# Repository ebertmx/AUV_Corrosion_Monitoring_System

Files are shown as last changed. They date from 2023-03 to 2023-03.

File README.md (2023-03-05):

# AUV_Corrosion_Monitoring_System
 Autonomous Corrosion Monitoring System for AUV Deployment

 See Final_Report for full project description.
 See Engineering_Analysis for engineering techniques and simulation result
 See Project_Background for intial research and motivation.

Sample Images
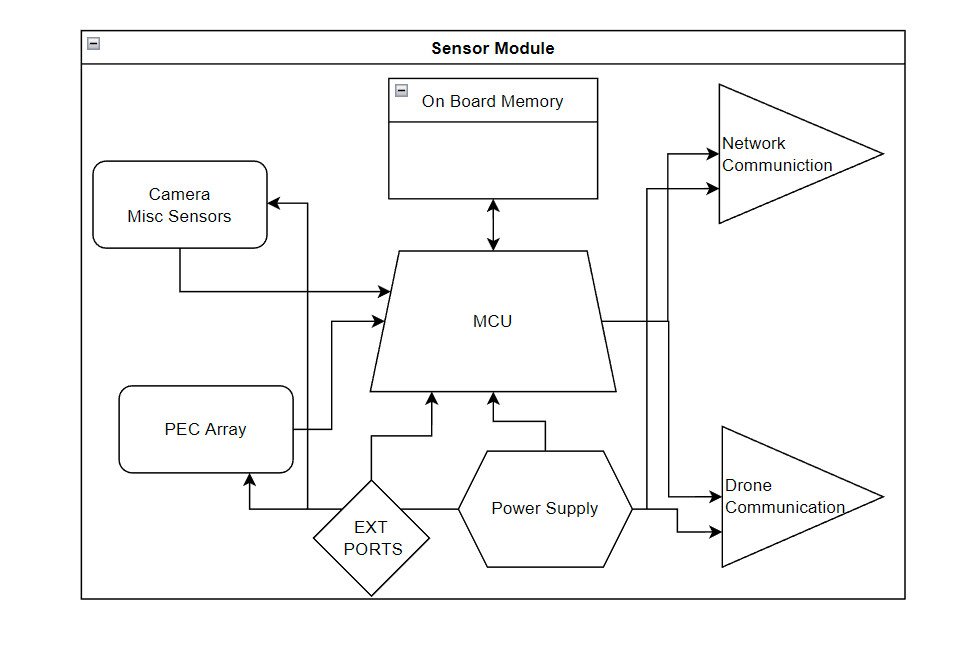
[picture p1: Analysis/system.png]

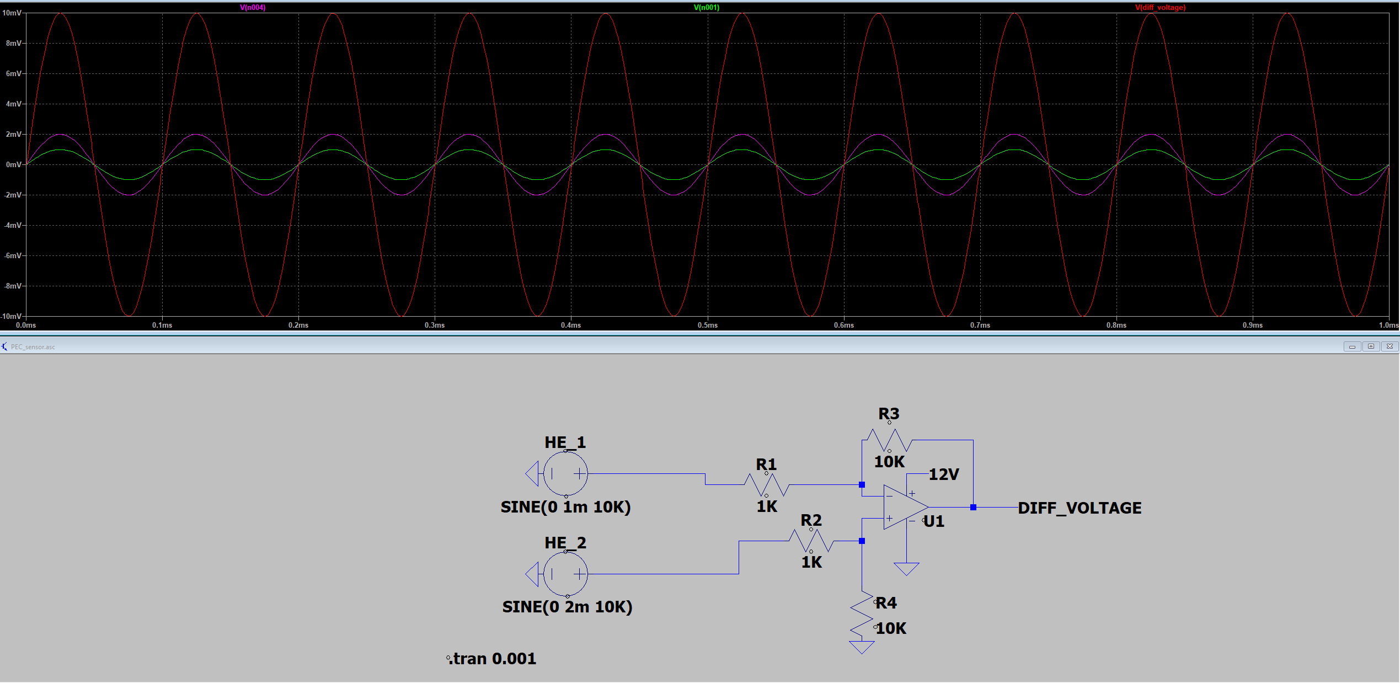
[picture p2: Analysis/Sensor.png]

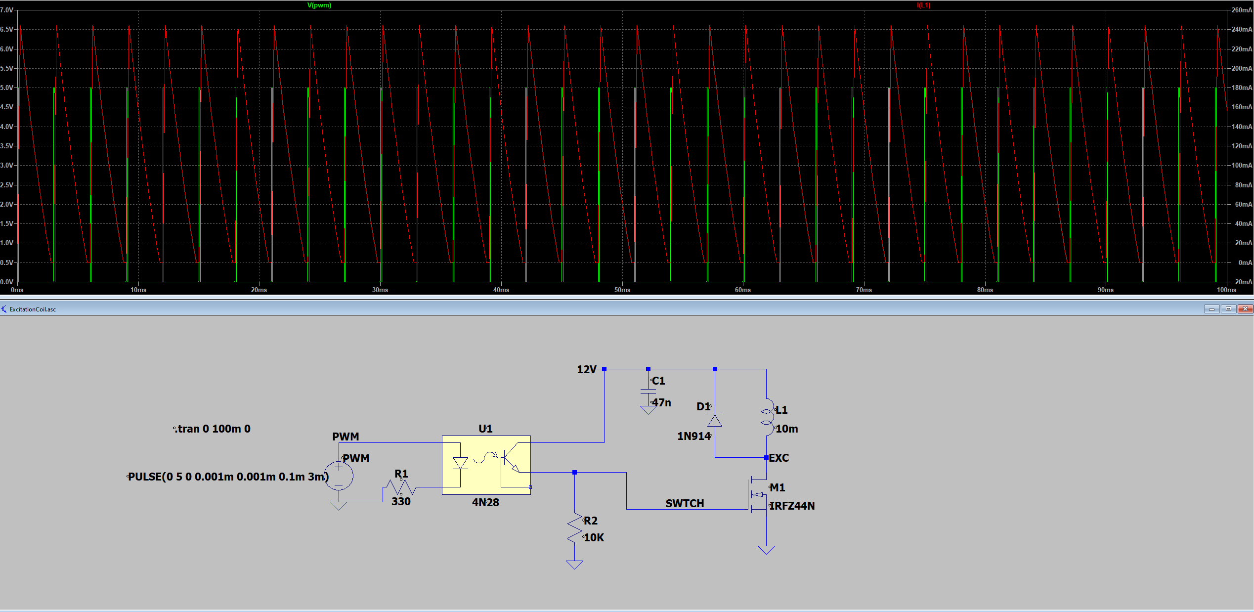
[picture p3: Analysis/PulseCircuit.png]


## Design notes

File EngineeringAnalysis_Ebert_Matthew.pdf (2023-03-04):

# Engineering Analysis

Underwater Drone Sensor Package

Matthew Ebert; V00884117

2022-NOV-10

ENGR 446 Report

## Contents

Figure 8: Simulated excitation inductor circuit for PEC sensor unit. Green plot shows pulses from PWM controller.

I.

GLOSSARY

PEC | Pulse Eddy Current
CDS | Corrosion Detection System
UW | Underwater
HE | Hall Effect
PWM | Pulse Width Modulation
ADC | Analog Digital Converter
EC | Eddy Current
SMU | Sensor Module Unit
CU | Command Unit
RU | Relay Unit
MCU | Microcontroller unit
PCU | Power Control Unit

II. PROPOSED SOLUTION

This solution consists of sensor module units (SMU) installed on AUVs, air-water communication relay nodes (RN), and a centralized command unit (CU).

A. System Description

The sensor modules collect data and communicate with both the drones and central command. The relay’s possesses transceivers for both radio and water communications that allow for underwater sensor modules to communicate with the land-based command unit. Below is an example deployment scenario.

A harbor purchases several drone systems and equips them with sensor modules. Relay devices are installed on piers to give communication coverage throughout the harbor. The relays communicate via Wi-Fi to the central command unit and use an underwater sonic/laser communication method to communicate with the sensor modules. The sensor modules use mesh network technology to increase the signal and range of underwater communications.

Directed by the CU, the sensor modules control their respective drones to systematically scan new and moored vessels for corrosion. All data is saved and processed at the CU. AI algorithms are employed on the new and archived data to enhance the detection capabilities of the system. A few employees monitor and review to finding of the system. Harbor members and boat owners pay a monthly subscription to regular scan and updates from the system on the health of there hulls which pays for the system.

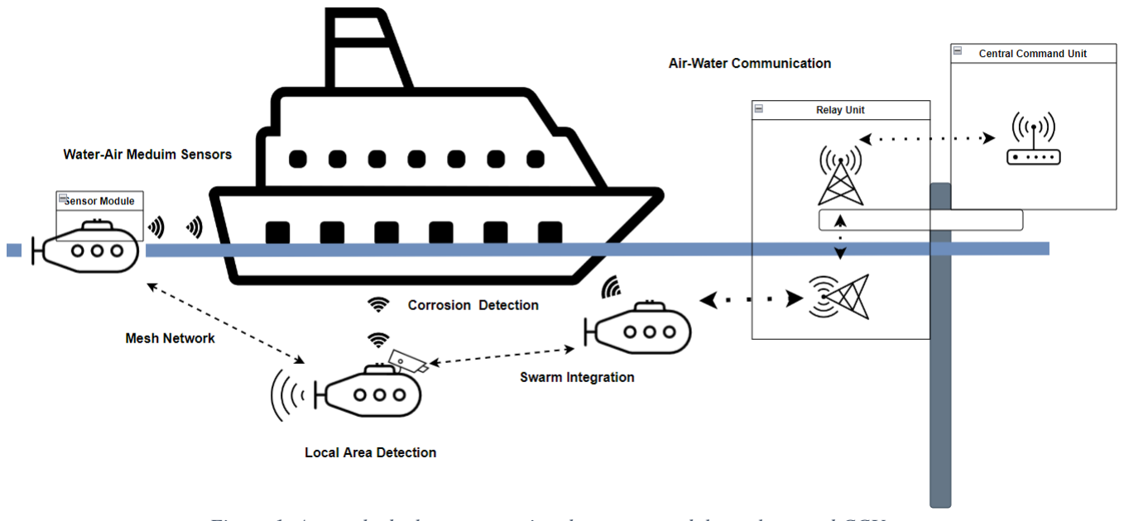
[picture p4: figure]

Figure 1: A sample deploy system using the sensor modules, relays, and CCU.

The focus of this analysis is on the SMU and corrosion detection from an autonomous drone. Other aspect of the system will be considered in a later report.

1) Sensor Module

The focus of this report is the sensor module. Figure 2 shows the component breakdown.

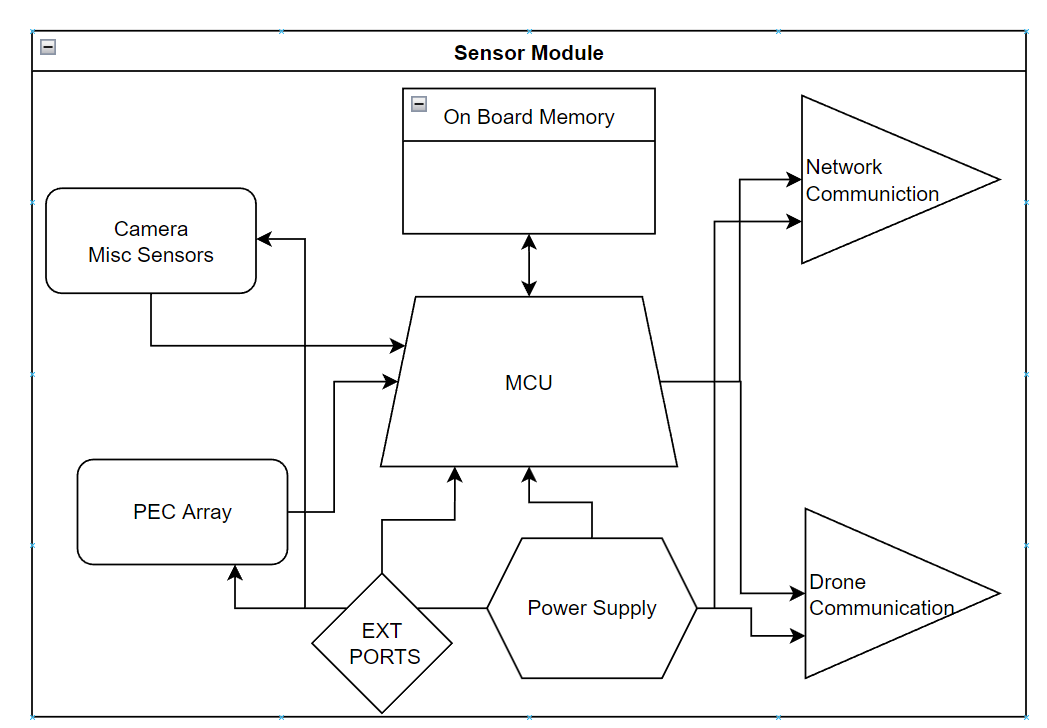
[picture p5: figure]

Figure 2: Sensor module system diagram. *PEC: Pulse Eddy Current

The MCU handles all processes within the SMU. It has communication links with the system network and the drone itself. The MCU has external ports (EXT PORTS) which allow a wired connection with an external computer or peripheral device. The onboard memory is for local data storage and backup storage in case of network communication failure. The camera and misc.sensor unit are to assist in navigation, obstacle avoidance, and manual override of a human operator.

2) PEC Array

The pulse eddy current (PEC) array is the primary unit of the sensor module and the focus of this report. The PEC array system model is shown in Figure 3.

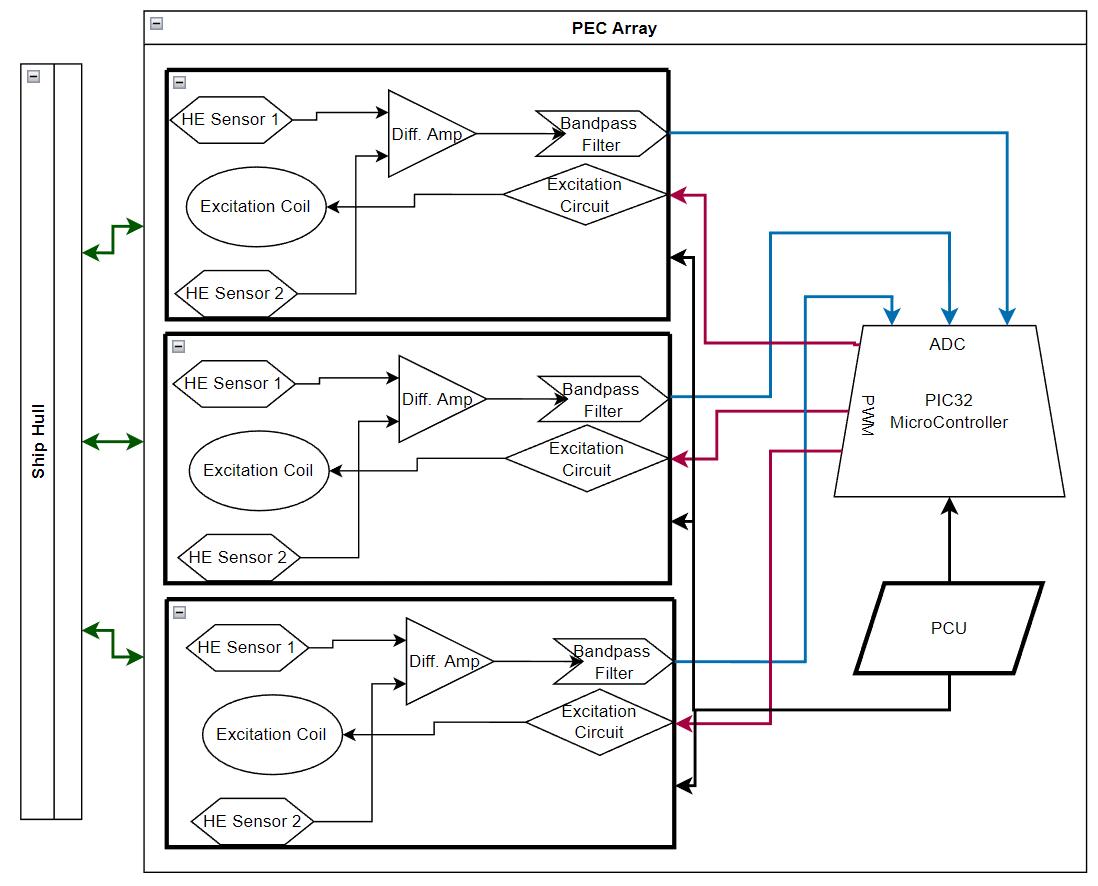
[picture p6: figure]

Figure 3: PEC array system. The array is made of one or more PEC detection units (Figure 4).

The PEC array consists of multiple instances of the PEC detection Unit (Figure 4). Each unit can detect corrosion in its area of effect. The area of effect of an individual unit is small (~40mm); consequently, an array of these devices will be used to create a large scan field.

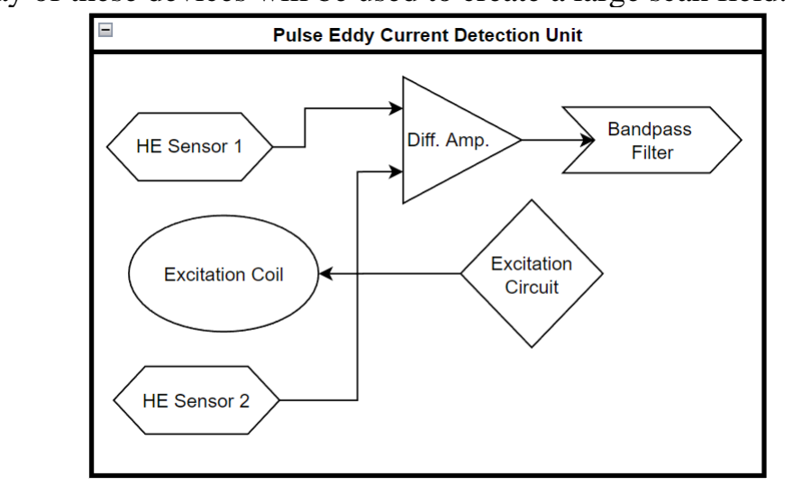
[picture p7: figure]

Figure 4: PEC detection unit

A description and analysis of each component in the PEC detection unit is covered in Section III.

III. ENGINEERING ANALYSIS

The PEC array is primary unit of the sensor module. Other component may be purchased OTS and require little analysis. A custom design is required for the PEC array to function on an AUV. Consequently, the engineering analysis will focus on this component.

A. Pulse Eddy Current Hardware Design

The PEC sensing device will include
1. An excitation coil
2. 2 Hall Effect sensors
3. A PWM excitation circuit
4. An amplifier circuit
5. A bandpass filter
The 2 HE sensor allow for a differential measurement. A differential measurement can reduce the need for a reference signal and make the sensor more versatile [1].
a) Pulsed Eddy Current Detection Theory [1]

EC detection uses an AC-driven inductor to induce eddy currents in a conducting sample. The induced eddy currents vary around flaws or defects in the conducting material. A magnetic sensor can detect these currents and variations. The penetration depth of these signals is related to the frequency of the driving signal as shown in the equation below [1].

δ is the penetration depth at 1/e reduced density, ω is frequency, μ is magnetic permeability, and σ is electrical conductivity. Traditional EC uses a sinusoidal input at a given frequency. With only one excitation frequency, the sensor is limited to one penetration depth distribution. Alternatively, many frequencies (and therefore depths) can be expressed if a modulated square wave drives the inductor. The Fourier transform and power spectra of a pulsed square wave demonstrates this property (Figure 5 and Figure 6). This is known as pulsed eddy current detection (PEC).

Figure 5: Pulse waveform in time and frequency domain [1]

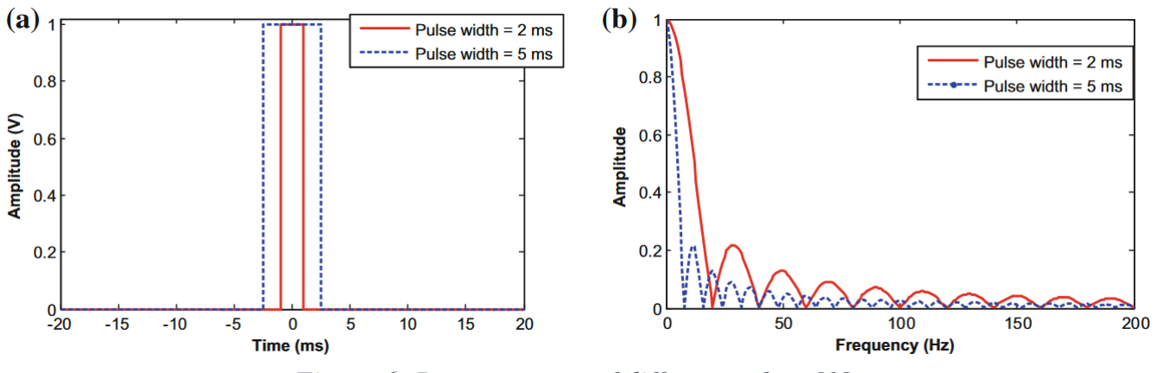
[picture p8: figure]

Figure 6: Power spectra of different pulses [1]

With PEC, the input wave may be modulated to achieve different depths and apply varying power to the inductor coil. Varying the pulse width also eliminates the need for a reference signal
[2] (Figure 7).

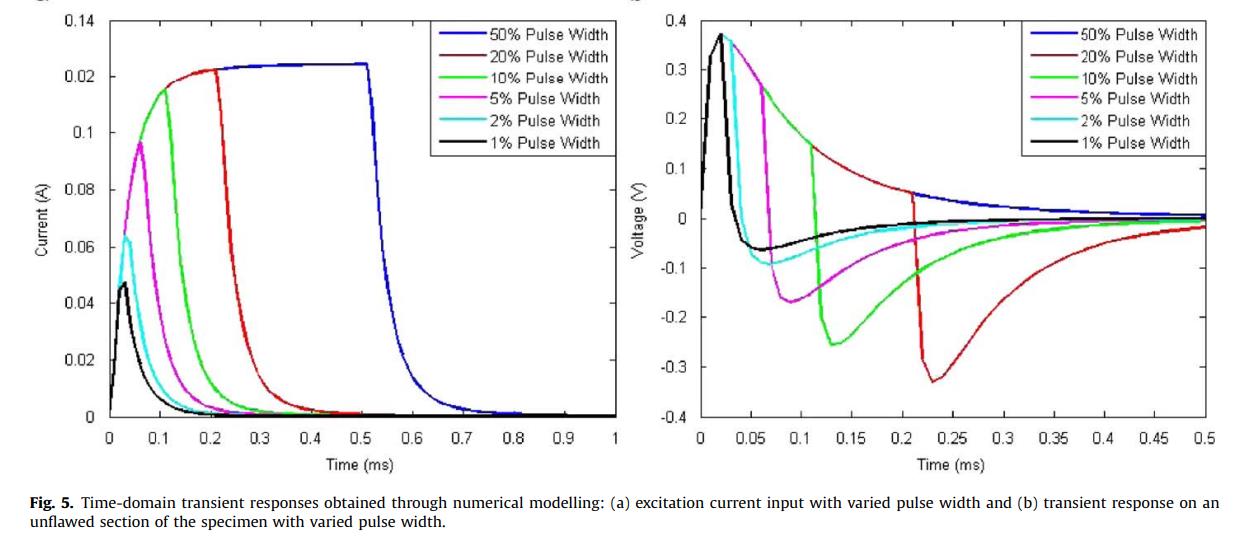
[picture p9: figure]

Figure 7: Simulated transient response of PEC [2]

2) Hall Effect

Magnetic sensors are commonly used at the detector for a PEC system. These devices detect the coupled magnetic field induced by the driving coil. This field is directly proportional to the eddy currents in the material.
Hall Effect (HE) sensor have the sensitivity requirements and are commonly used in this application [1], [3]. The governing equation for a HE sensor is
VHE = K B
Where K is a constant coefficient specific to the device and B is the magnetic field density.
3) Excitation Circuit

Figure 8 shows the current response in the excitation coil to PWM input from a microcontroller.

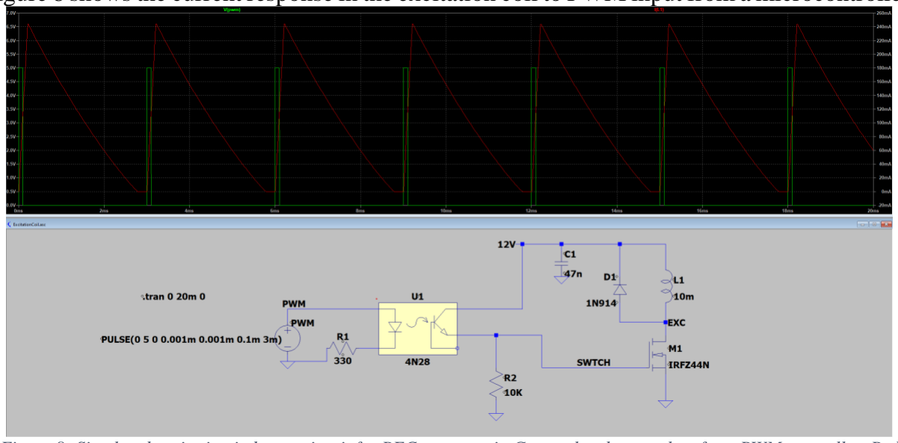
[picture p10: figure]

Figure 8: Simulated excitation inductor circuit for PEC sensor unit. Green plot shows pulses from PWM controller. Red show inductor current (peak 245mA).

An optocoupler (4n28) is used to isolate the microcontroller from the high-power inductor circuit.
A IRFZ44N NMOS transistor was selected to control the current to the excitation coil L1. The IRFZ44N is fast switching and has a drive voltage of 10V [4].
The 10mH inductor was selected as an overestimation place holder.
The 1N914 diode is place to drain the stored energy of the inductor to reverse power surge back through the NMOS. The 1N914 is fast switching and can dissipate 500mW of power. With a peak power surge from the inductor of
Ppeak = Imax ∗ Vdrop = (250mA ∗ 1V) = 250mW , we have a 2x safety factor for the component.
The capacitor C1 is for filtering of noise from 12V supply line. It may be tuned as necessary.
a) Resonance analysis

C1 and L1 in the above circuit form a parallel resonance circuit. Although, the supply voltage is DC, the PWM control creates an AC response. For the current values, the resonance frequency was calculated as

fresonance =

1

2π(LC)

1
2

= 7.341kHz

Since the pulse frequency of PEC system falls between 80kHz and 1MHz, the circuit should not enter resonance during operation.

4) Amplifier Circuit

Figure 9 shows the designed differential amplifier circuit and it’s simulated response to input from HE sensors.

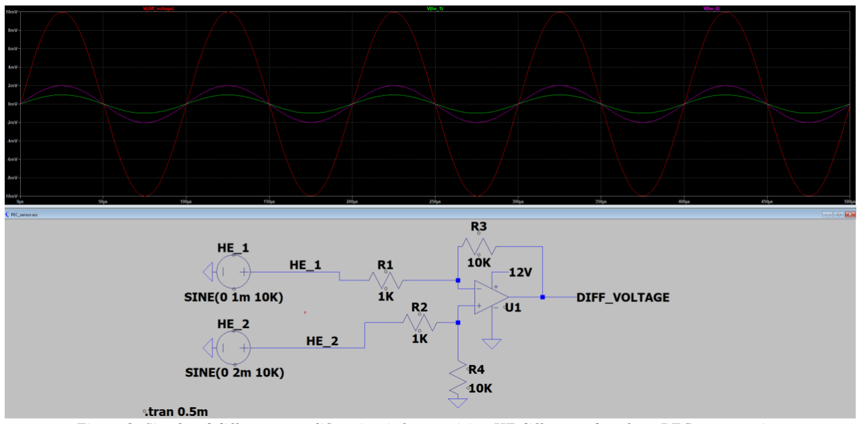
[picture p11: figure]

Figure 9: Simulated difference amplifier circuit for acquiring HE difference data from PEC sensor unit.

The amplification of this circuit from input to output adheres to
Vout = Vin ∗ (

R3
R1

) , if R1 = R2 and R3 = R4.

The exact amplification needed is unknown at this time. Testing will reveal the amplification needed from the response of materials and sensor units. The gain can be adjusted easily through substitution of the sensors above and will be adjusted until the output range falls between 0 and 3.3V (based on microcontroller ADC voltage [4]).

5) Bandpass Filter

A bandpass filter will be needed at the output of the amplifier to mitigate noise cause by the sensor devices, power regulators, and the op amp itself. Testing is needed to determine the precise range of frequencies to filter, but the design will take the form of Figure 10.

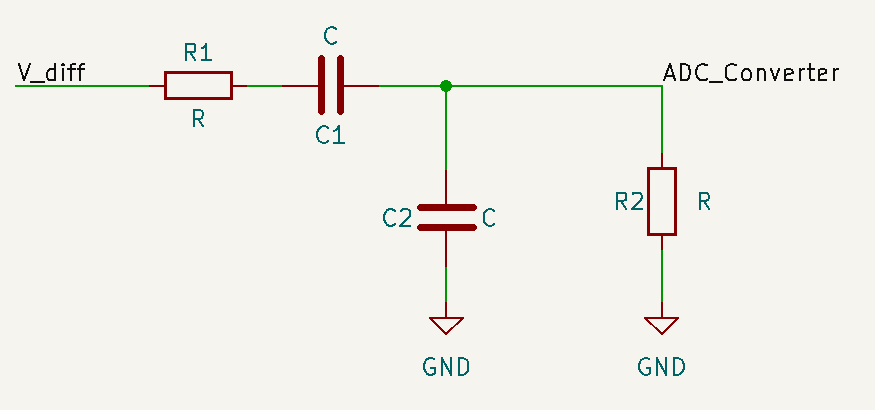
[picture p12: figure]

Figure 10: Bandpass filter design

The high and low cut off frequencies and band width equation for this circuit are fℎ =

1
2πR1C1

fl =

1
2πR2C2

BW = fℎ − fl
6) PEC Array

An array of PEC sensor units will be used to increase the scan area of the system. Each PEC unit will contain 2 HE sensor, an excitation coil, and the circuits described above (PWM control, difference amplifier, and bandpass filter). Each unit will be positioned as shown in Figure 11. A nominal lift off distance of 3mm was selected based on work from Kral J. which showed a decreased sensor response above 4mm [6].

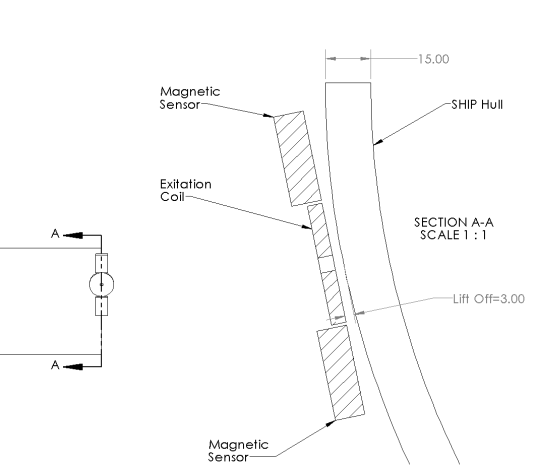
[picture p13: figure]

Figure 11: PEC unit scanning position on ship hull.

An array will be formed to maximize spatial resolution of HE sensors (Figure 12). The exact spacing may change if test reveal closer or farther spacing is required based on the excitation coil effect and HE sensitivity.

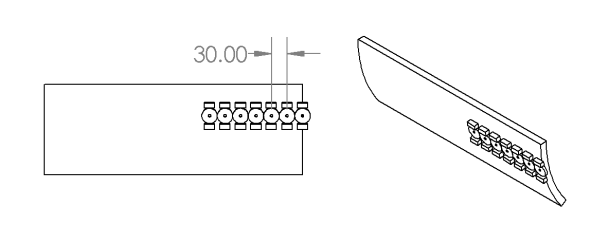
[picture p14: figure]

Figure 12: PEC array configuration

B. Microcontroller

The preliminary selected microcontroller is the PIC32MZ2064DAS176 [5]. This micro was selected for the properties
- 45 channel ADC (12-bit): To read data from DAC
- 9 PWM Modules (250ns resolution): To control excitation circuit
- Integrated Graphics Processor: For fast data processing and AI implementation
- 200MHz clock speed: High speed processor for Real-Time functionality
- 128MB externally addressable DDR2 DRAM: Large RAM for data processing
- 5 SPI and 6 I2C modules: Interfaces for other peripheral devices.

This PIC32 device operates between 2.6 and 3.3V and requires a maximum of 500mA [5].

C. Power and Charging

The power needs of the system will change with additional peripherals including the wireless communication system. However, estimation may be made using common devices. The considered devices and their electrical specification are shown in Table 1. This table assumes 12 PEC detection units in the system. 12 units with a 40mm spacing covers 0.36m. This matches with some standard lengths of small underwater drones and AUV’s [7].

Table 1: Electrical Characteristics of Components

Component | DC Operating Voltage (V) | Max Current (mA) | Power (W)
PIC32MZ2064DAS176 | 3.3 | 500 | 1.65
PEC Array (12 units) | 12 | (245)*12 (Figure 8) | 35.28
UW-COM Unit | - | - | 2.6W [8]
Under Water Camera | | | 15.4W [9]
Additional Components* | | | 10W (Generic)
| | TOTAL | 64.88W
* Other components are unknown at this time; however, compared to the main devices they will consume significantly less power. 10W is allocated as a large buffer.

64.88 W is the absolute maximum power draw of this system. A battery is selected with appropriate head room to extend the life of the system and operating time. The CSB HRL 1280W battery can provide 12V at 80W and has dimension small enough to mount to a AUV. Based on the data sheet, the battery could sustain 65W for over 90min [10]. The operating time may be less than this due to the pulsing power draw of the PEC array.

IV. DISCUSSION

The PEC array is the primary component of the sensor module and the focus of this analysis. Other components, such as underwater communication, have been addressed and are available for purchase [11]. A large portion of the final design will be software control and data analysis; however, an effective corrosion detection system is needed before these can be developed.

A. Detection Method

PEC detection offers many advantages over tradition EC detection. PEC can easily scan multiple depths in a surface with a single frequency pulse. Since the excitation signal is a pulse rather than a sinusoid, PWM signals from a microcontroller can control the sensor without the need for a sinusoidal function generator.

B. Component selection

A HE sensor is a common and widely used device. Equipment such as coils or magnetoresitive devices exist, but these have additional requirements or supporting hardware to function [1]. Some Magnetoresitive devices such as giant magnetoresistance (GMR) have been shown to have higher accuracy or lower noise. Should the HE be ineffective at these devices will be considered as a substitute.

The differential amplifier and filter circuit are common data acquisition circuits and need no comment.

The NMOS transistor may be ‘overkill’ for the performance requirements of the system. However, will allow multiple coils to be driven from the same circuit, potentially decreasing complexity and components. With a 200mA draw up to 50 coils could be driven by this transistor. Heat management will be essential in this configuration, and no more than 25 coils is recommended to maintain a 2x safety factor.

The inductor chosen for simulation has an inductance of 10mH. Likely, the actual value of the inductor will be significantly lower. Tests will show the required magnetic flux density to achieve the needed induced signal strength. Should a smaller inductor be needed, the driving voltage may need to be reduced to limit the current. A buck converter and filter circuit would serve this purpose. The power requirement of the PEC array will also decrease in this case.

A note should be made while programming the PWM input to the excitation circuit due to the potential resonance hazard. Frequency below 20kHz should be avoided as the resulting low impedance may result in unknown behaviour or damage.

C. Microcontroller selection

The main reason for selecting the PIC32 microcontroller was the large number of ADC channels and PWM outputs. The size of the array will require many HE sensors. Should the resolution requirements exceed the 45 channels available on the microcontroller, a switching methodology can be adopted. The array can be split into several sub array with enable switches. Multiple HE sensor can be wired to the same ADC port and read with a switching algorithm. The integrate graphics processor on the PIC32 will allow for fast data and image processing. Real-time decision can be made locally with the analysis of this data and video feed.

D. Power Calculations

The value of 250mA used for the PEC system in Table 1 is an extreme maximum estimation. This current would be drawn if the excitation inductor was left fully power for more than 0.5ms. Since these inductors will be pulsed, the average current over time will be significantly lower and with proper capacitor usage, might be reduced significantly. This value will vary depending on the pulse width selected but will always be less than the full 250mA.

E. Recommendations

The next step in development will be to test the PEC array system. A Prototype should be built with the maximum value of components to collect initial data from corroded and non corroded samples. Based on these results the system can be tuned to the desired resolution and signal strength through iteration.

V. REFERENCES
[1] A. Sophian, G. Tian, and M. Fan, “Pulsed Eddy Current Non-destructive Testing and Evaluation: A Review,” Chin. J. Mech. Eng., vol. 30, no. 3, Art. no. 3, May 2017, doi: 10.1007/s10033-017-0122-4.
[2] I. Z. Abidin, C. Mandache, G. Y. Tian, and M. Morozov, “Pulsed eddy current testing with variable duty cycle on rivet joints,” NDT E Int., vol. 42, no. 7, pp. 599–605, Oct. 2009, doi: 10.1016/j.ndteint.2009.04.001.
[3] P. Ripka and M. Janosek, “Advances in Magnetic Field Sensors,” IEEE Sens. J., vol. 10, no. 6, pp. 1108–1116, Jun. 2010, doi: 10.1109/JSEN.2010.2043429.
[4] “IRFZ44NPBF,” Digi-Key Electronics. https://www.digikey.com/en/products/detail/infineon-technologies/IRFZ44NPBF/811772 (accessed Nov. 09, 2022).
[5] “PIC32MZ2064DAS176 | Microchip Technology.” https://www.microchip.com/en-
us/product/PIC32MZ2064DAS176 (accessed Nov. 09, 2022).
[6] “(PDF) The Lift-Off Effect in Eddy Currents on Thickness Modeling and Measurement.” https://www.researchgate.net/publication/260304181_The_Lift-Off_Effect_in_Eddy_Currents_on_Thickness_Modeling_and_Measurement (accessed Nov. 07, 2022).
[7] “CHASING M2 ROV | Professional Underwater Drone with 4K UHD Camera - GPS
Central.” https://www.gpscentral.ca/product/chasing-m2-rov-professional-underwater-drone-with-4k-uhd-camera/ (accessed Nov. 09, 2022).
[8] “W-MK-21025-1_M64.pdf.” Accessed: Nov. 09, 2022. [Online]. Available: https://www.waterlinked.com/hubfs/Product_Assets/Modem_M64/W-MK-21025-1_M64.pdf?hsLang=en
[9] “iAQUA-100Z <div class="category_title">Underwater Full HD Zoom Lens PoE Network Camera</div>,” INDUSVISION. http://www.indusvision.com/project/iaqua-100z-underwater-full-hd-zoom-lens-poe-network-camera-2/?lang=en (accessed Nov. 09, 2022).
[10] “CSB HRL1280W 12V 80W High Rate Long Life Battery,” AtBatt. https://www.atbatt.com/csb-hrl1280w-12v-80w-high-rate-long-life-battery-11/ (accessed Nov. 09, 2022).
[11] “LUMA,” Hydromea. https://www.hydromea.com/underwater-wireless-communication (accessed Nov. 10, 2022).

Appendix A. PROJECT BACKGROUND

# Marine Monitoring Sensor Package: Project Background

Matthew Ebert; V00884117

2022-OCT-21

University of Victoria

ENGR 446

## Contents

I. Background | 3
A. Underwater Marine monitoring | 3
B. Corosion monitoring | 3
C. Underwater Unmanned Vehicles | 5
II. Objective | 5
A. Problem | 5
B. Purpose | 6
C. Aims | 6
D. Limitations | 6
III. Potential Solutions | 6
A. Harbor/Port Wireless Based Swarm (Drone Linked) | 6
B. Ship based drone with wired package | 7
C. Dedicated Tow Fish (Vessel Only) | 7
D. Large array position by multiple or large vehicle | 7
IV. Initial Assessment | 7
A. Criteria | 8
B. Ratings | 8
V. References | 10
Figure 1: Underwater monitoring drone from Blueeye Robotics [2] | 3
Figure 2: Ultrasonic reading from corroded aluminium plate [12] | 4
Figure 3: Eddy Current Corrosion Detection [11] | 5
Figure 4:DT640 hull crawler detection system [3] | 5
Table 1: Available Corrosion Detection Technology | 4

I. BACKGROUND

Almost 70% of the planets surface is covered by oceans. From energy generation to commerce, the oceans are an essential part of human society. However, this environment is known for its harshness on materials and equipment. Steel is greatly affected by exposure to salt water by corrosion. Since most ocean assets are constructed with steels, this creates an enormous maintenance cost for ocean activities. In the early 2000’s the cost of corrosion was estimated a 3.1 percent of the USA’s GDP [1].

A. Underwater Marine monitoring
To combat corrosion and the other degrading effects of the ocean such a marine growth, detection techniques and constant monitoring is required. Historically, this inspection process was accomplished with dive teams or, in extreme scenario’s, dry docking. In recent times, underwater drones, remote operated vehicles (ROV’s), and autonomous underwater vehicles (AUV’s) have become the more popular method of inspection. The drone system currently available have several sensors, but tend to require manual control, lack certain sensor systems, and consist of specialized configurations [2] [3]. Figure 1 show an example of the current monitoring drones available.

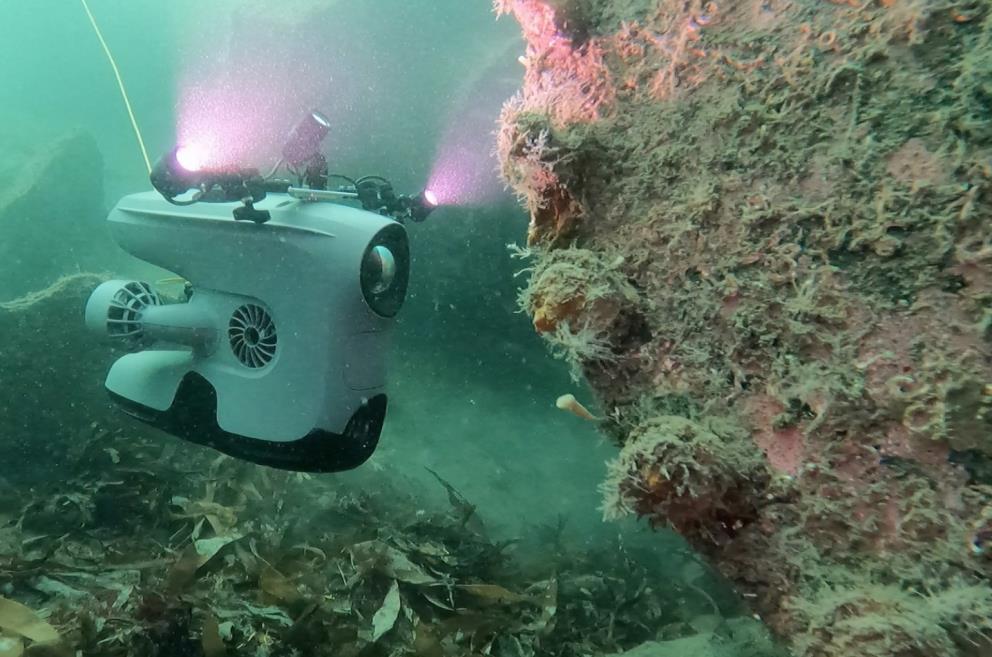
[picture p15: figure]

Figure 1: Underwater monitoring drone from Blueeye Robotics [2]

Thus, there is a market for modifiable, autonomous, and efficient marine monitoring system

B. Corosion monitoring
Perhaps the most sought-after monitoring system for marine equipment is for corrosion. Aqueous corrosion is constant, inevitable, and can be difficult to detect [4]. Several methods exist to detect corrosion. For monitoring in an ocean environment, these methods must work in and out of water, and detect beneath protective coatings [5]. Additionally, these methods must be nondestructive in nature. The available technology which fit these requirements are summarized in Table 1.

Table 1: Available Corrosion Detection Technology

Type | Description
Ultrasonic | Use ultrasonic emission in the water to detect different hull compositions at close range [5], [6]. Example sensor feedback shown in Figure 2.
AI based Visual inspection | Use AI and other algorithms to enhance non-invasive sensing equipment detection [7]
IR heat mapping | Use thermal wave propagation and infrared temperature field measurements to observe variation in coated steel [8].
Laser profilometry | Non destructive evaluation of a material surface profile to detect and monitor corrosion [9]
Magnetic Flux Leakage | Use magnetic coils to induce and measure magnetic fields in material to detect defects [10]
Eddy Current Detection | Use a probe and inductor to induce and measure magnetic eddy currents in materials and identify defects [11]. Example use shown in Figure 3.
Electrode Probe | Test the resistivity of the material via 2 electrodes to test for corrosion. Note requires a contact probe.

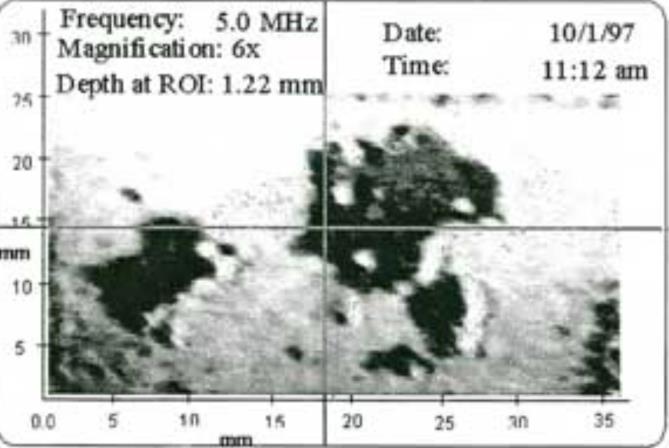
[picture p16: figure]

Figure 2: Ultrasonic reading from corroded aluminium plate [12]

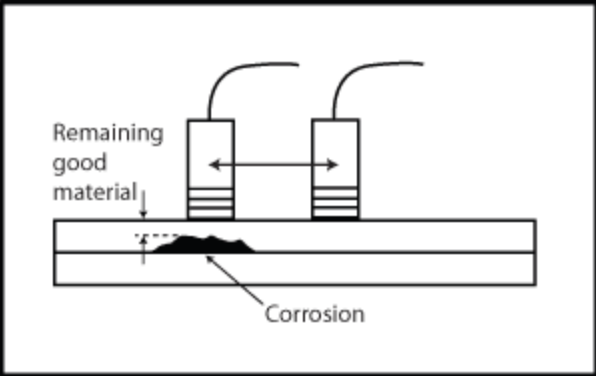
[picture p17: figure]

Figure 3: Eddy Current Corrosion Detection [11]

While these methods have proved viable for corrosion detection, work needs to be done to deploy this technology in an autonomous mobile system.

C. Underwater Unmanned Vehicles

Many underwater drones, ROV’s, and AUV’s exist for maneuvering inspection, and autonomous behaviour in the ocean. These range from remote operated tethered ROV’s for focused inspection to magnetically attached hull crawlers [3], [13]. The broad selection of these devices more than meets the mobility needs of a static monitoring environment (such as a docked ship or ocean turbine). Therefore, a sensor and control system are needed for deployment on these vehicles.

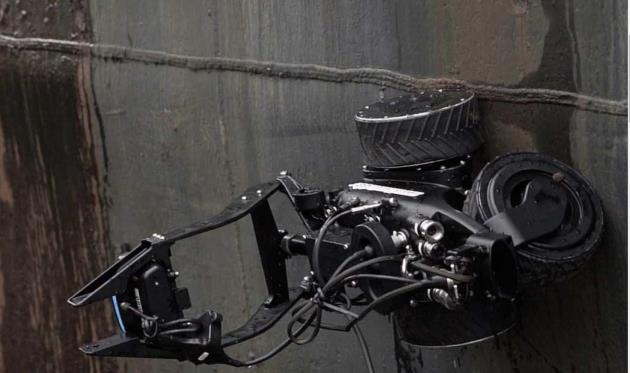
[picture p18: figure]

Figure 4:DT640 hull crawler detection system [3].

II. OBJECTIVE

A. Problem
An online (real-time), integrated, and low management marine monitoring system is needed to combat corrosion and other degradation effect on marine assets. Corrosion in early stages is difficult to detect due to surface coating and large exposed areas of marine equipment. The battle against corrosion is constant and expensive. With a real-time and automated detection system, ocean equipment may be monitored constantly. This will increase the odds of early detection and prevent the need for manual inspection of hulls, potentially reducing corrosion cost significantly. Underwater drone and drone swarm technology has the mobility and capacity to achieve these goals; however, there is a need for an adaptable sensor array and data analysis system which can be deployed using the available drone technology.
B. Purpose
The objective of this work is to design a commercially producible sensor package which may be mounted to existing underwater drone technology. This system should scan marine assets for corrosion and damage, coordinate with multiple instances or devices, and analyze data for online display. Additionally, the system must offer an advantage over current marine monitoring technology in terms of speed, scale, and human resources.
C. Aims
The aims of this project are to develop a sensor package that:
1. Detects corrosion and defects on marine devices, vessels, and structures
2. Is configurable for specific needs and situations
3. Deploys and integrates on underwater drones, ROV’s, AUV, and similar vehicles
4. Links with devices over a network to coordinate large scale monitoring
5. Does not require human attention while completing normal operation.

The scope of this report covers primarily aims 1 and 2.

D. Limitations
The capabilities of the mounted vehicle will not be considered unless extreme needs present themselves because they are assumed not to be the limiting factor. Additionally, the vehicle software interface is assumed to be compatible with the final design. Detection through excessive organic or other debris will not be considered since this is variable and requires additional attention. The project will be based on previous work and literature. Additional analysis may include:
- Communication range and throughput
- Power requirements
- Sensor range and required clarity.

III. POTENTIAL SOLUTIONS
All solution must integrate a variety of sensors for corrosion, damage, marine growth, and visual inspection. Different user may have different requirements regarding the monitoring needed; thus, the package must be modular in nature and allow for custom configuration. Additionally, since available power and communications on drone systems cannot be guaranteed, the system must be independent of the drone itself.

The difference in solution presents itself in terms of deployment and use case.

A. Harbor/Port Wireless Based Swarm (Drone Linked)
One solution includes a fleet of drone equipped with the sensor package. In this solution the drone is slaved to the sensor package itself. Communication with a central control and movement commands are handled by the sensor package and relevant instruction relayed to the drone.

Communication buoys would span the area of interest to allow for underwater wireless communication relay between the drones and a central control center.
The drones would systematically scan docked vessels, equipment, and structures with an algorithm to maximize scan time. Multiple drones may work squads to minimize the time each boat spend under inspection.
The drones would have a local hub to return for recharge and maintenance. Central control could also override the basic algorithm for high priority scans of vessels and objects.
B. Ship based drone with wired package.
This solution is for medium or large vessels which may set anchor outside of ports or harbors. This also applies to structure such as offshore oil rigs of wind turbines. These vessels would have one or multiple drones equipped with a sensor package. These systems would be tethered to the ships from which they may receive power and communication. The drones would be deployed at certain time when the vessel is stopped. They would quickly follow set paths to scan the entire ship and send data back to the command unit. This command unit may also be off site if a satellite or cellular network is available.
C. Dedicated Tow Fish (Vessel Only)
This device would operate constantly as the vessel is in motion. Attached to a tether, a tow fish would house the sensor package and adjust itself slowly across the entire hull of the ship. The tow fish would communicate and be powered through the tether connection to maximize deployed time. The difficulty of this method is obtaining accurate measurements with the disturbance of the vessel in motion. This system requires the ship to be in motion for positioning. Thus, it is not feasible on stationary platforms or structures.
D. Large array position by multiple or large vehicle
This system would attach multiple drones to a single, large, sensor package. The package would be positioned and moved under and along vessels and equipment and complete a scan in a few slow passes. The idea for this device is maximizing scan width and minimizing number of passes to decrease time for complete scan coverage.

IV. INITIAL ASSESSMENT
To select a potential solution, a weighted decision chart will be created with several criteria. These criteria will target qualities of a solution that will most fully meet the non functional requirements of the product. The primary non functional requirements of the product are
1. Product improves speed of detection for corrosion and other ailments on marine assets
2. Product can be configured for a specific task with different sensors and equipment.
3. Product reduces human resources needed to preform this task.
4. Product offer an advantage over current means of detection and monitoring through ease of use, quality of results, or quantity of scanning (total surface area scan per unit time).

A. Criteria

The following criteria will be weighted in order. The exact weights will be determined exactly when the discrepancy between the solutions is known.

The first criteria of this assessment will determine the types of viable sensing equipment for the solution. Should only some of the methods be usable (i.e. Only magnetic flux and eddy current), the ability of the system to fully detect and monitor will be examined closely. Since a requirement is configurability, a system that limits the available sensor will also receive a penalty.

The second selection criteria rates a systems autonomy and human resource needs. Should a system require a lot of attention it will receive a lower score than a one with lots of autonomy.

The 3rd criteria determines which solution would most effectively scan an entire vessel/platform completely once. This rating will help measure the potential speed of a solution.

The 4th selection criteria attempts to rate the scalability of a solution. This will consider the change in scenario from one to several vessels or platforms and compare the hardware, software, and maintenance requirements of the system.

The 5th criteria observes the potential operating times of the solution. If a solution only usable for small windows of time, it will receive a lower score than one available more of the time.

The 6th criteria will be a qualitative estimate of how easy the system may be to use and maintain. This may be subjective to the individual completing the assessment and thus will have the lowest weighting.

B. Ratings

Deployment
Method

Range =
[0,5]
Criteria | Autonomy | Score | Effective Scan | Score | Scalability | Score

Operating
time | Score | Maintenance | Score | Total
Weight | 0.3 | | 0.3 | | 0.2 | | 0.1 | | 0.1 | | 1
Harbor Swarm | 5 | 1.5 | 3 | 0.9 | 4 | 0.8 | 4 | 0.4 | 2 | 0.2 | 3.8
Ship Wired Drone | 3 | 0.9 | 2 | 0.6 | 2 | 0.4 | 1 | 0.1 | 4 | 0.4 | 2.4
Tow Fish | 3 | 0.9 | 1 | 0.3 | 3 | 0.6 | 4 | 0.4 | 4 | 0.4 | 2.6
Large Array | 2 | 0.6 | 5 | 1.5 | 1 | 0.2 | 2 | 0.2 | 2 | 0.2 | 2.7
Corrosion
Detection

Range =
[0,5]
Criteria | Range | Score

Detection
Depth | Score | Scalability | Score

Coverage
Area | Score
| | | | | | | | | Environment
Immunity | Score | Total
Weight | 0.2 | | 0.4 | | 0.1 | | 0.1 | | 0.2 | | 1
Eddy Current | 3 | 0.9 | 4 | 1.2 | 4 | 0.8 | 3 | 0.3 | 5 | 0.5 | 3.7
Ultrasonic | 3 | 0.9 | 5 | 1.5 | 2 | 0.4 | 3 | 0.3 | 1 | 0.1 | 3.2

Magnetic Flux
Leakage | 2 | 0.6 | 2 | 0.6 | 4 | 0.8 | 2 | 0.2 | 5 | 0.5 | 2.7
Electrode Probe | 0 | 0 | 3 | 0.9 | 5 | 1 | 5 | 0.5 | 5 | 0.5 | 2.9

Based on this analysis, a harbor swarm system with eddy current detection will be proposed.

V. REFERENCES
[1] G. H. Koch, M. P. H. Brongers, N. G. Thompson, Y. P. Virmani, and J. H. Payer, “Chapter 1 - Cost of corrosion in the United States,” in Handbook of Environmental Degradation of Materials, M. Kutz, Ed. Norwich, NY: William Andrew Publishing, 2005, pp. 3–24. doi: 10.1016/B978-081551500-5.50003-3.
[2] “Underwater | drone | technology | can | enhance | port | maintenance | | | HERE.”
https://www.here.com/learn/blog/underwater-drone-technology (accessed Oct. 24, 2022).
[3] D. | Trekker, | “DT640 | MAG | Utility | Crawler | For | Sale,” | Deep | Trekker.
https://www.deeptrekker.com/products/utility-crawlers/dt640-mag-utility-crawler (accessed Oct. 20, 2022).
[4] “Different types of corrosion on ships,” ShipInsight. https://shipinsight.comguide/different-types-of-corrosion-on-ships (accessed Oct. 24, 2022).
[5] M. Farin et al., “Monitoring saltwater corrosion of steel using ultrasonic coda wave interferometry with temperature control,” Ultrasonics, vol. 124, p. 106753, Aug. 2022, doi: 10.1016/j.ultras.2022.106753.
[6] T. Gao, H. Sun, Y. Hong, and X. Qing, “Hidden corrosion detection using laser ultrasonic guided waves with multi-frequency local wavenumber estimation,” Ultrasonics, vol. 108, p. 106182, Dec. 2020, doi: 10.1016/j.ultras.2020.106182.
[7] P. Karvelis, G. Georgoulas, V. Kappatos, and C. Stylios, “Deep machine learning for structural health monitoring on ship hulls using acoustic emission method,” Ships Offshore Struct., vol. 16, no. 4, pp. 440–448, Apr. 2021, doi: 10.1080/17445302.2020.1735844.
[8] R. Yang, Y. He, H. Zhang, and S. Huang, “Through coating imaging and nondestructive visualization evaluation of early marine corrosion using electromagnetic induction
thermography,” | Ocean | Eng., | vol. | 147, | pp. | 277–288, | Jan. | 2018, | doi:
10.1016/j.oceaneng.2017.09.023.
[9] H. Zhang and R. Wu, “An Investigation of Corrosion Progression Using Laser Profilometry,” in Studies in Applied Electromagnetics and Mechanics, G. Tian and B. Gao, Eds. IOS Press, 2020. doi: 10.3233/SAEM200028.
[10] “Magnetic Flux Leakage (MFL).” https://inspectioneering.com/tag/mfl (accessed Oct. 24, 2022).
[11] “Corrosion | Detection | and | Measurement | Using | Eddy | Current | Methods.”
https://www.olympus-ims.com/en/applications/corrosion-detection-eddy-current/ (accessed Oct. 24, 2022).
[12] “Detecting Hidden Corrosion.” https://www.machinerylubrication.com/Read/1363/detect-corrossion-oil (accessed Oct. 24, 2022).
[13] D. Trekker, “Underwater ROVs | Commercial Grade, Portable,” Deep Trekker.
https://www.deeptrekker.com/products/underwater-rov (accessed Oct. 24, 2022).

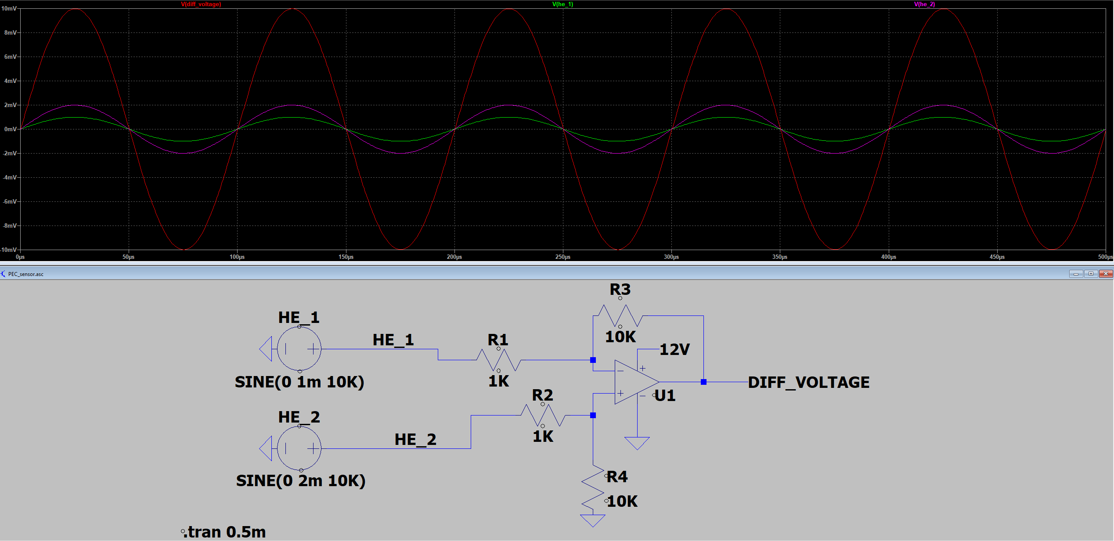
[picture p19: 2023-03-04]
Analysis/F.png

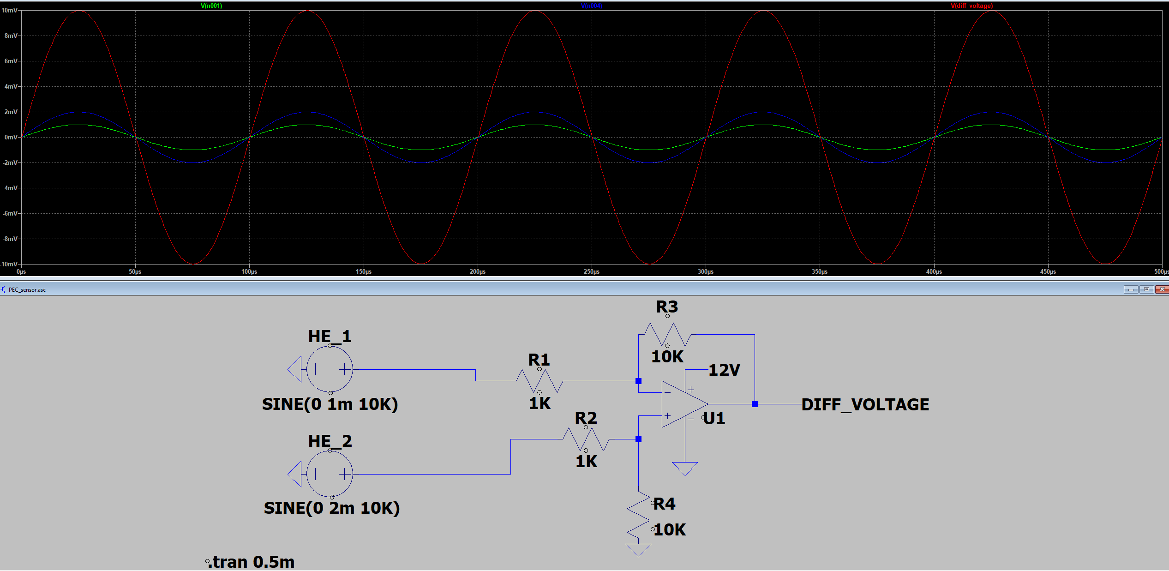
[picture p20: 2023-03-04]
Analysis/D.png

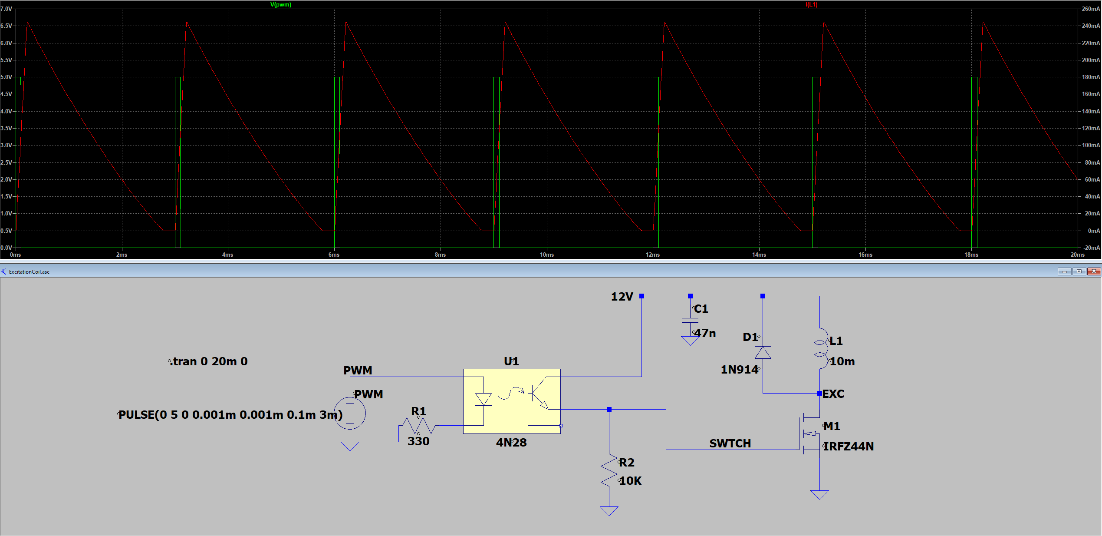
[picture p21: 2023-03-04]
Analysis/C.png

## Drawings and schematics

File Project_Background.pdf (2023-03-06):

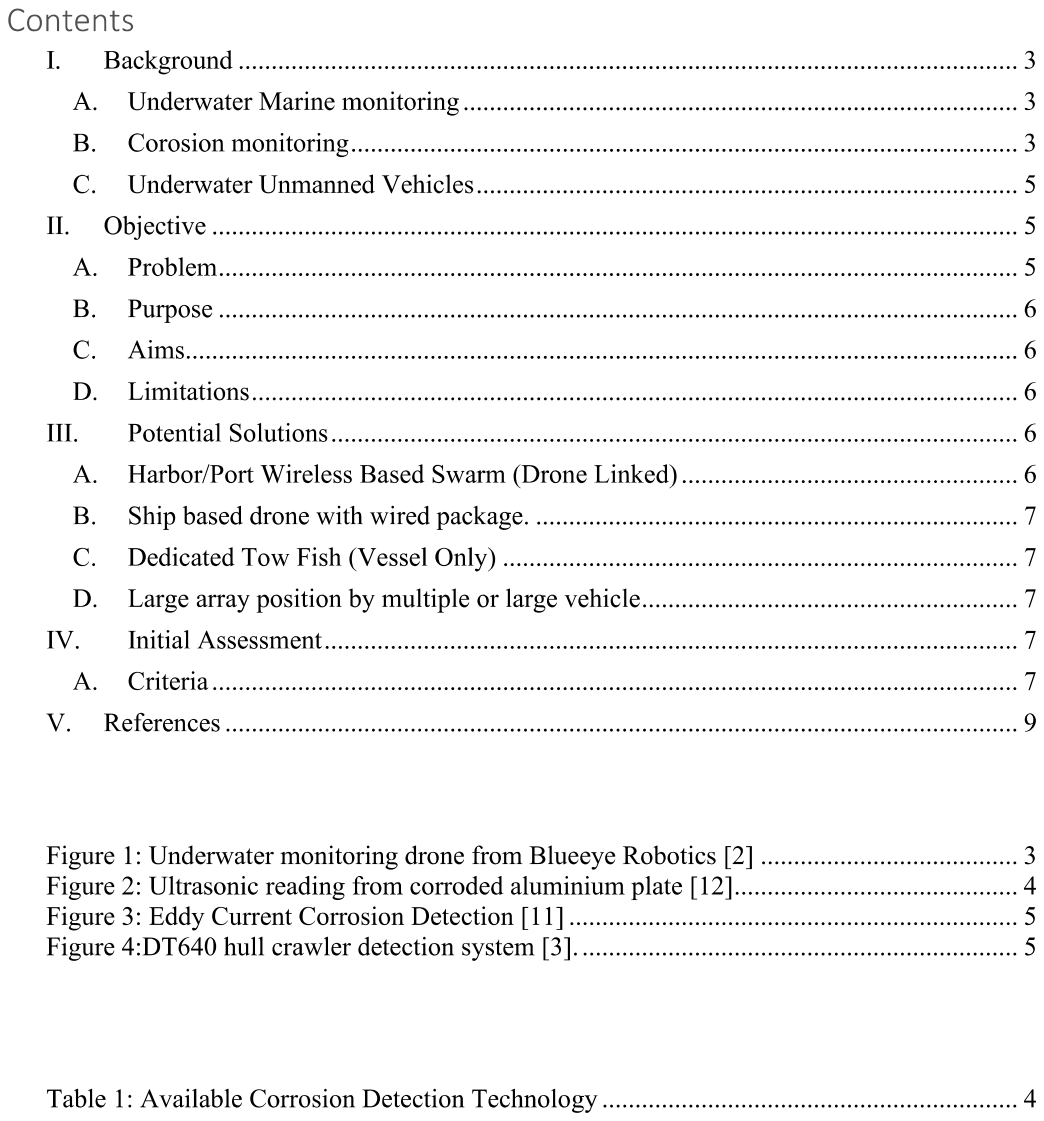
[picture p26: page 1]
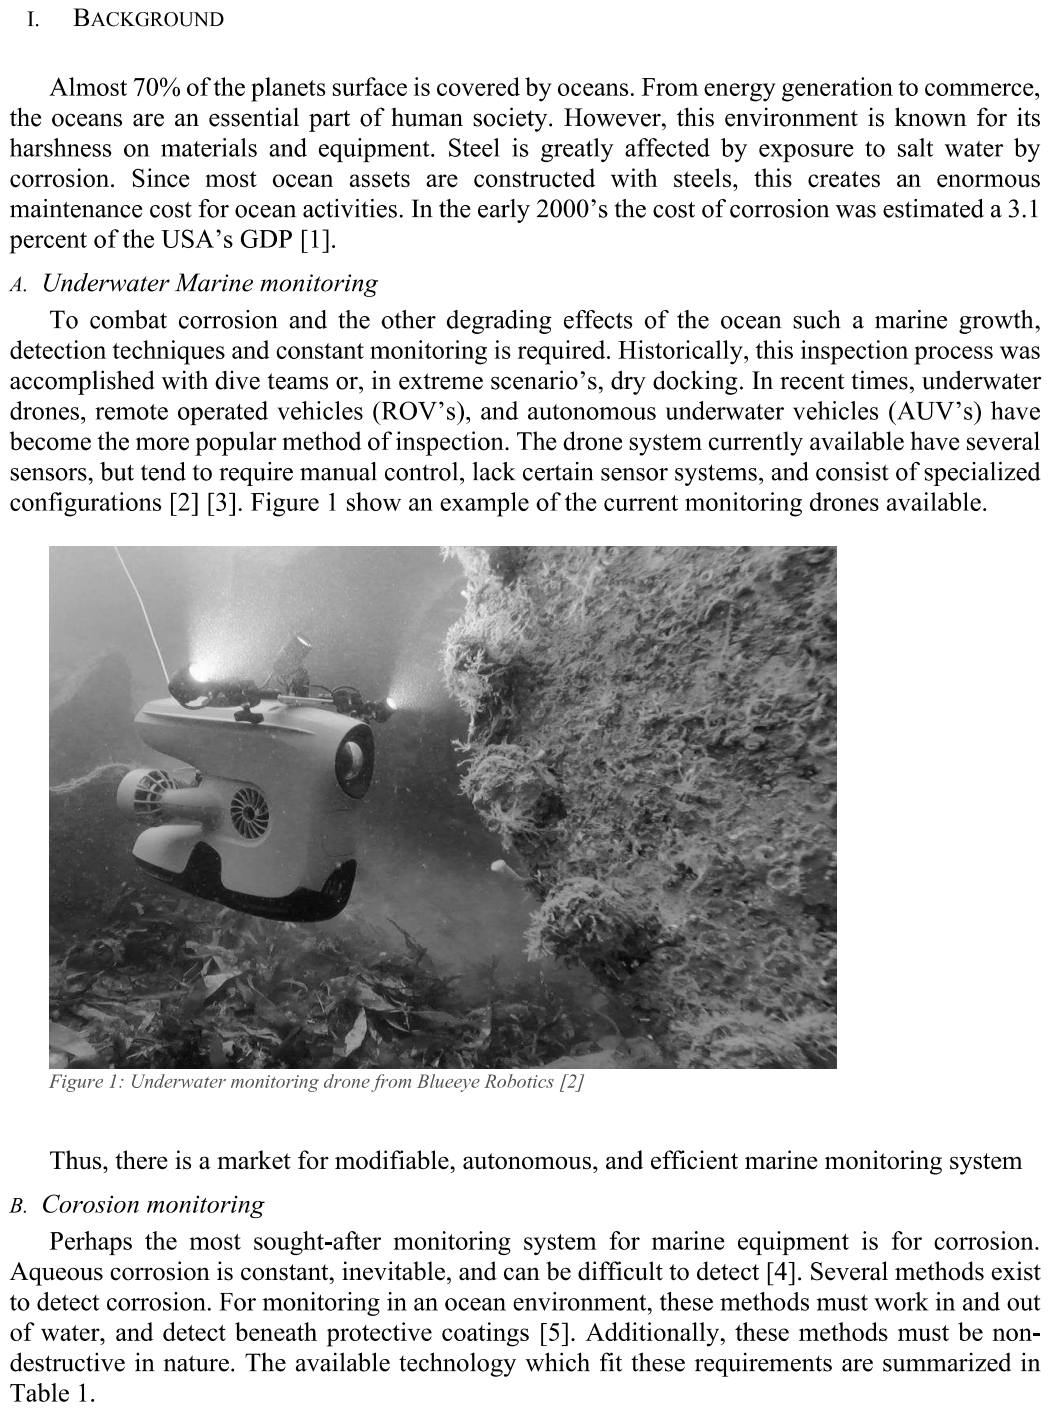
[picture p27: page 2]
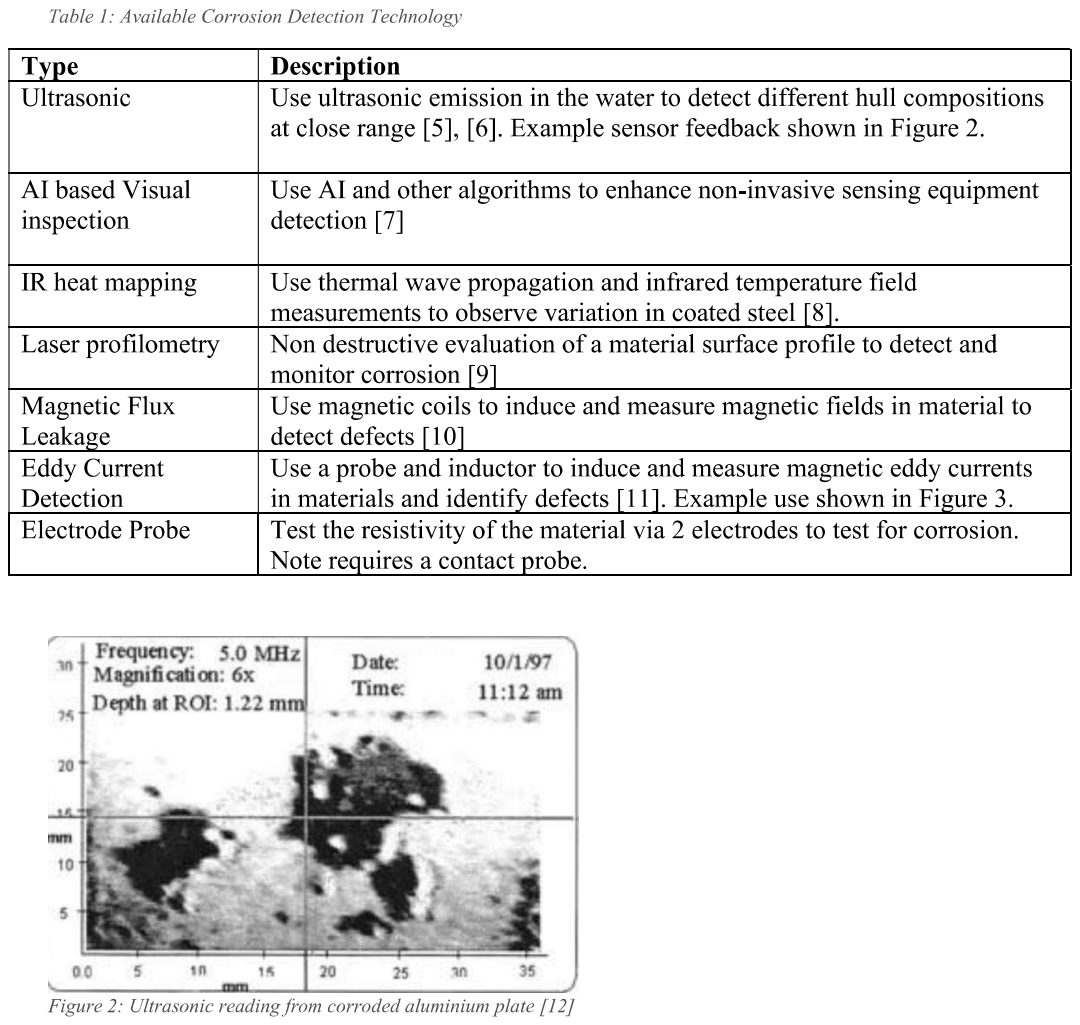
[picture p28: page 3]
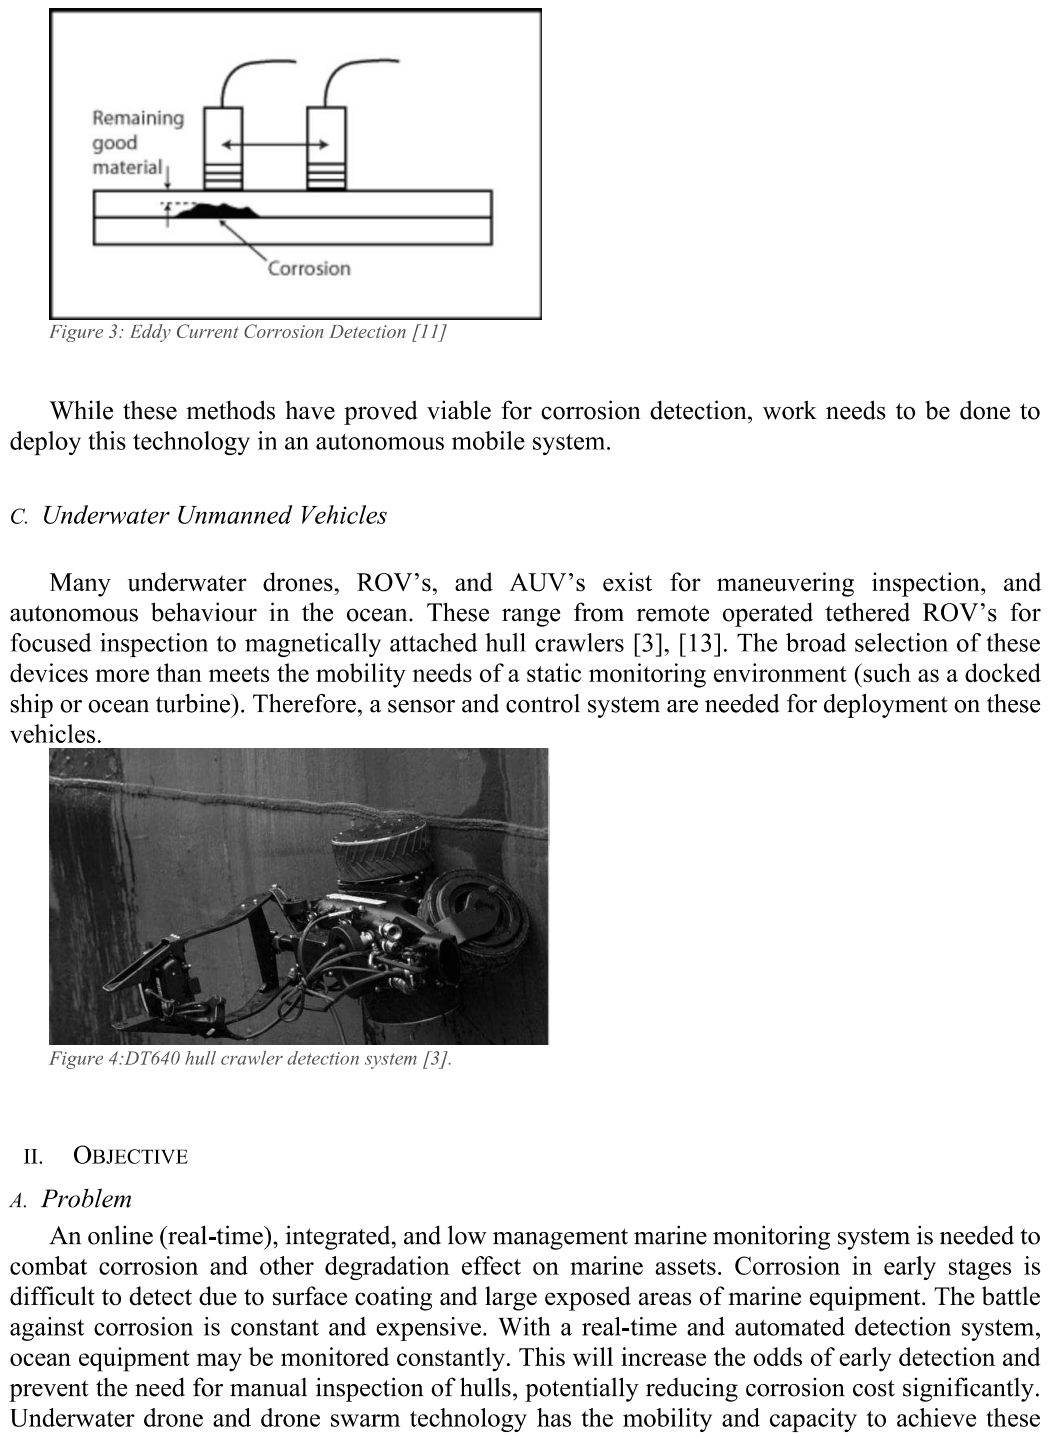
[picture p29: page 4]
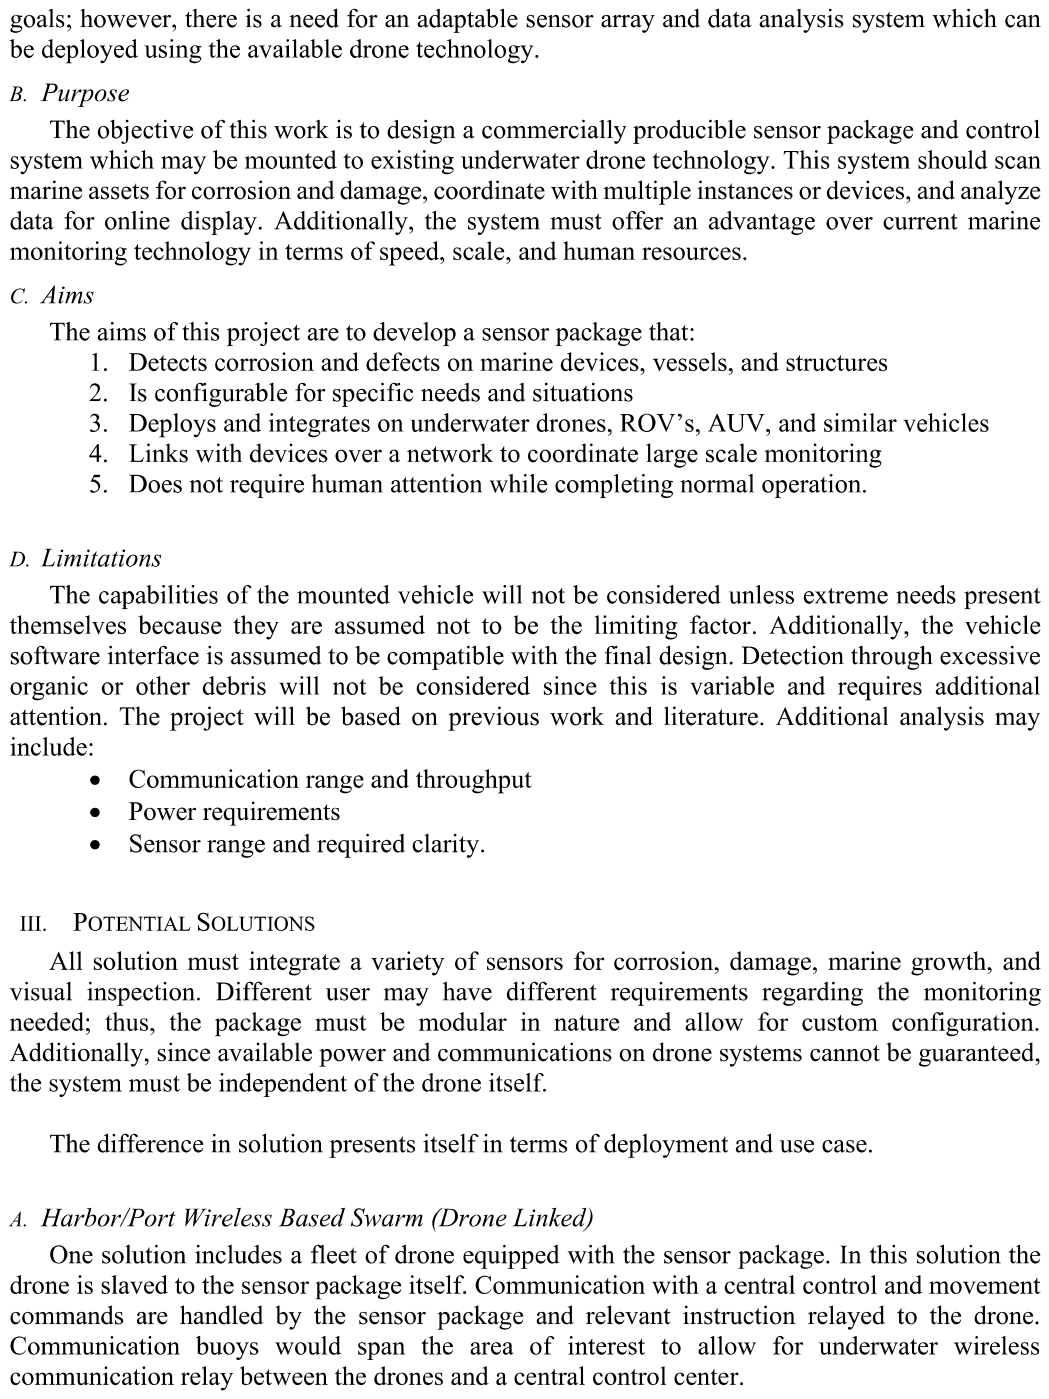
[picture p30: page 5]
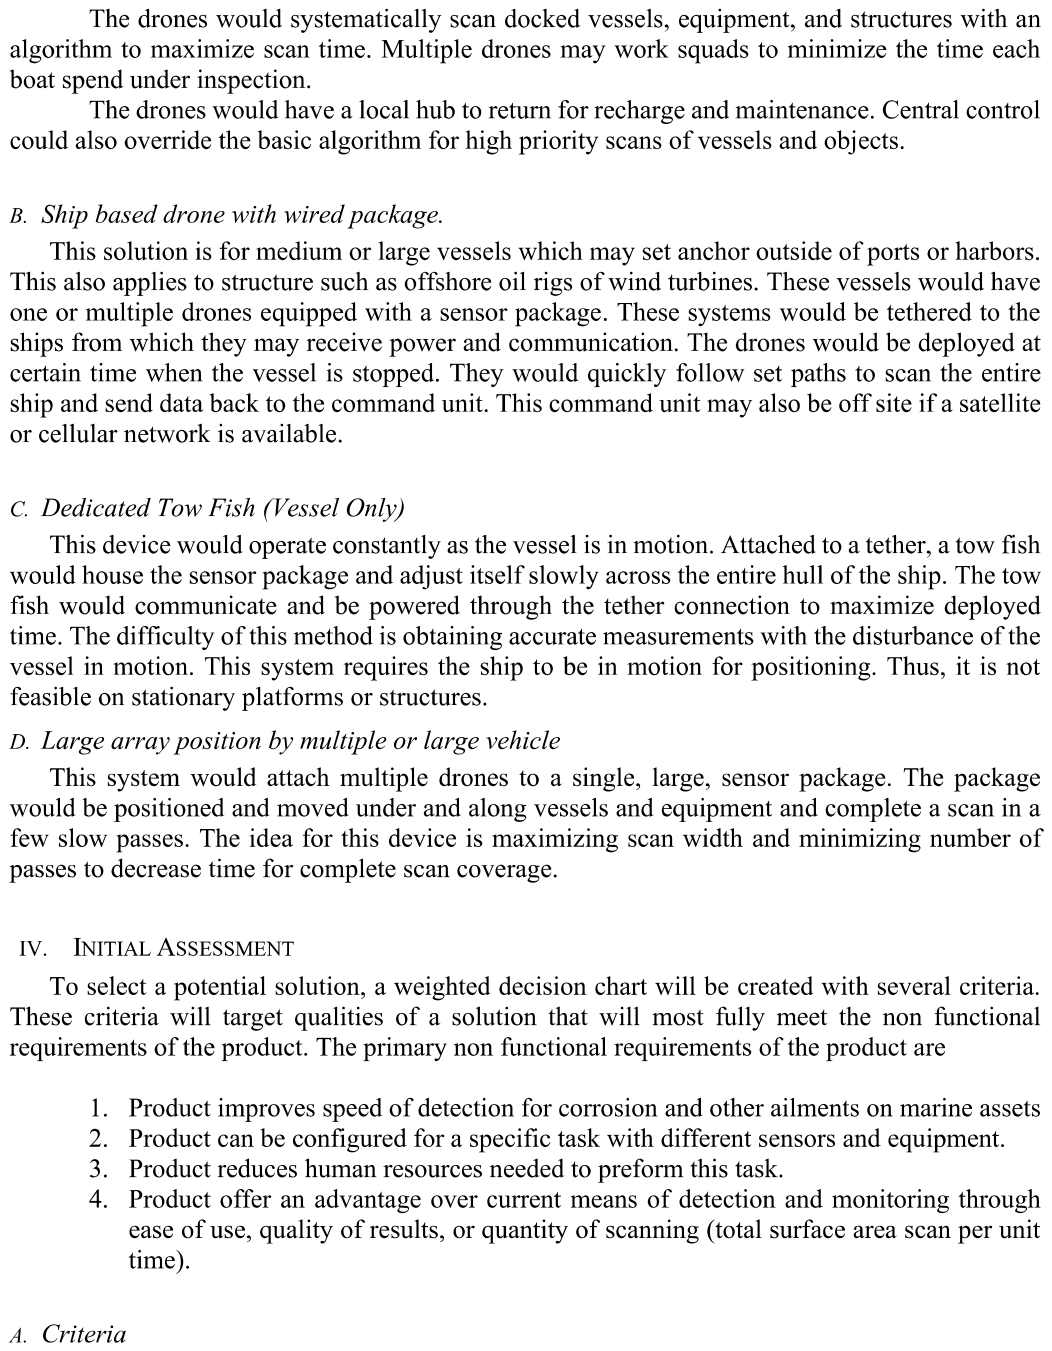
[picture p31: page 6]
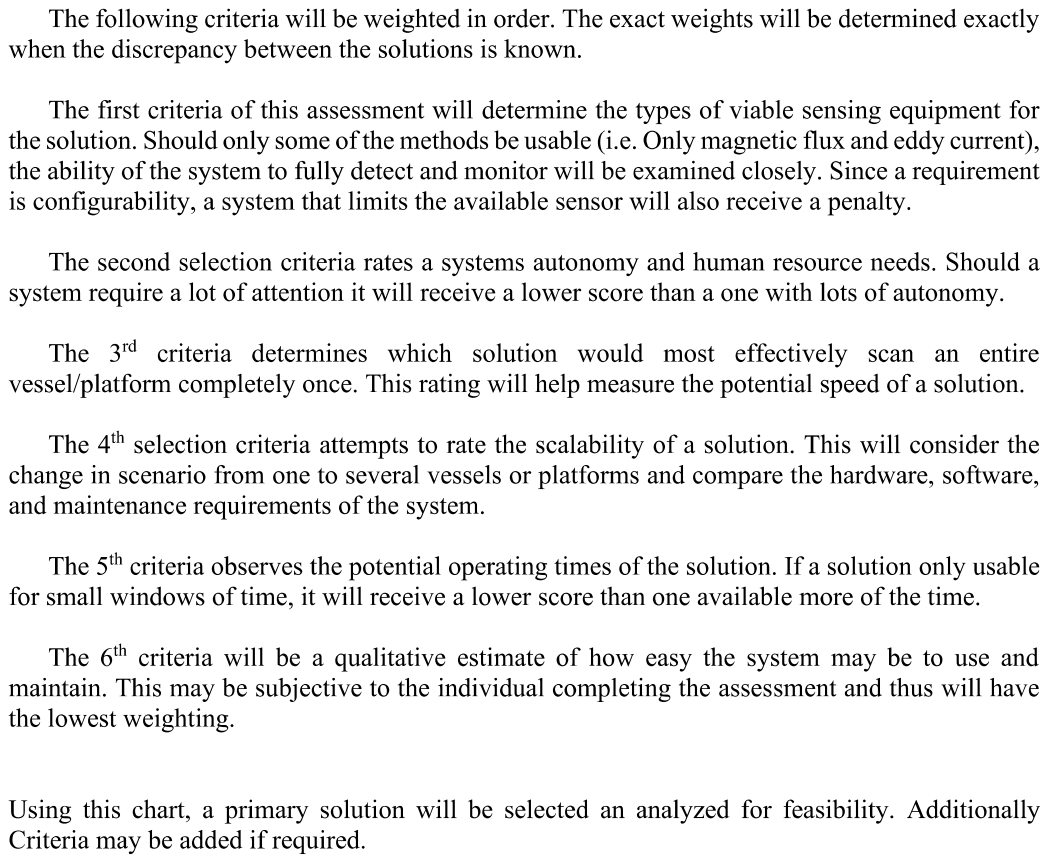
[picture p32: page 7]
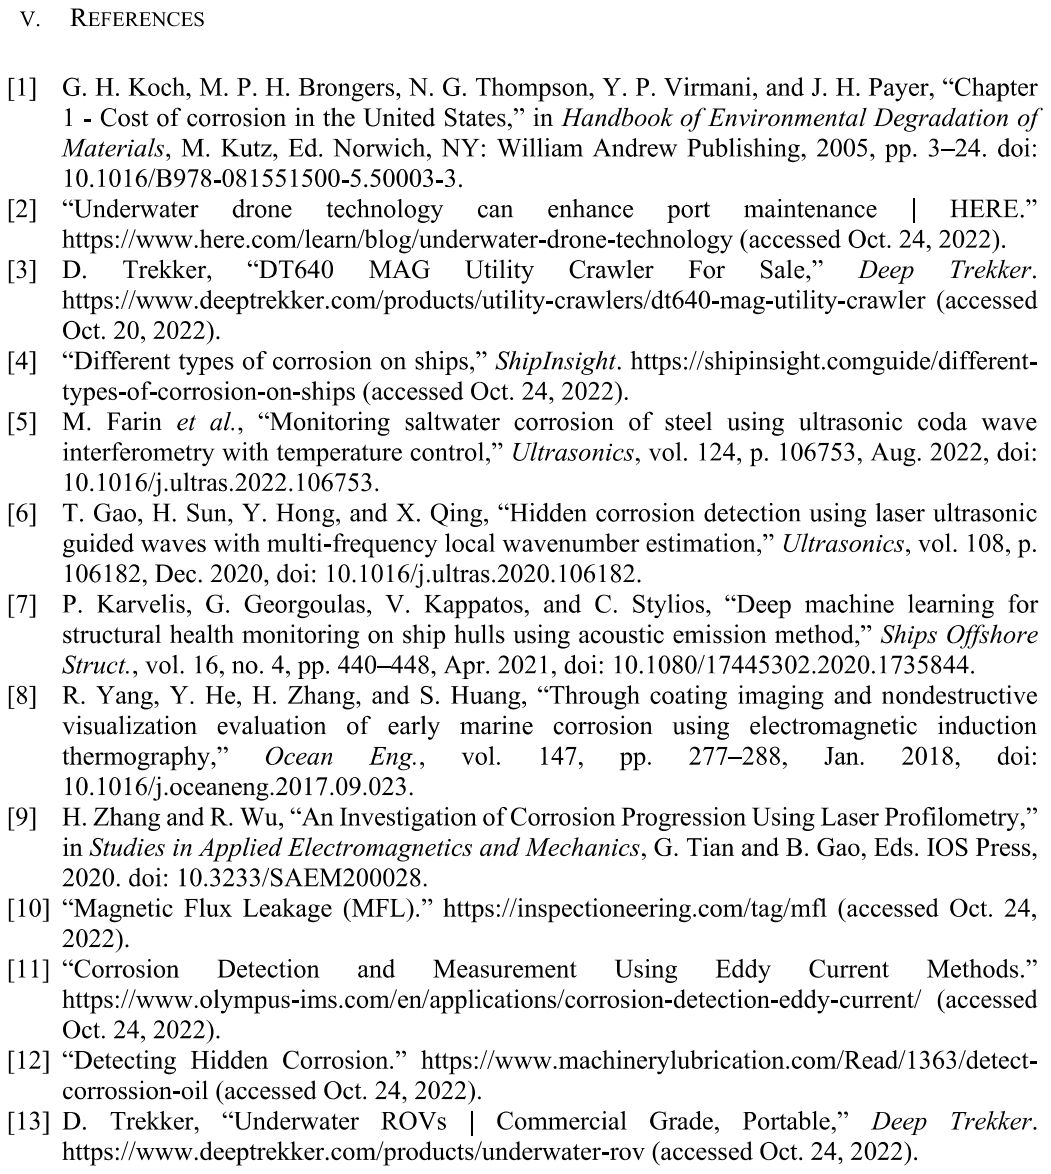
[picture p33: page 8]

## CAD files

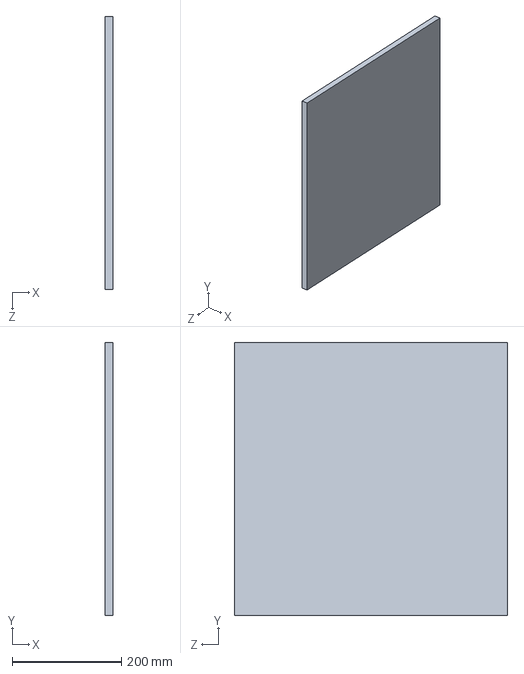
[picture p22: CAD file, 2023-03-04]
Analysis/straightHull.SLDPRT
15.0 x 500.0 x 500.0 mm

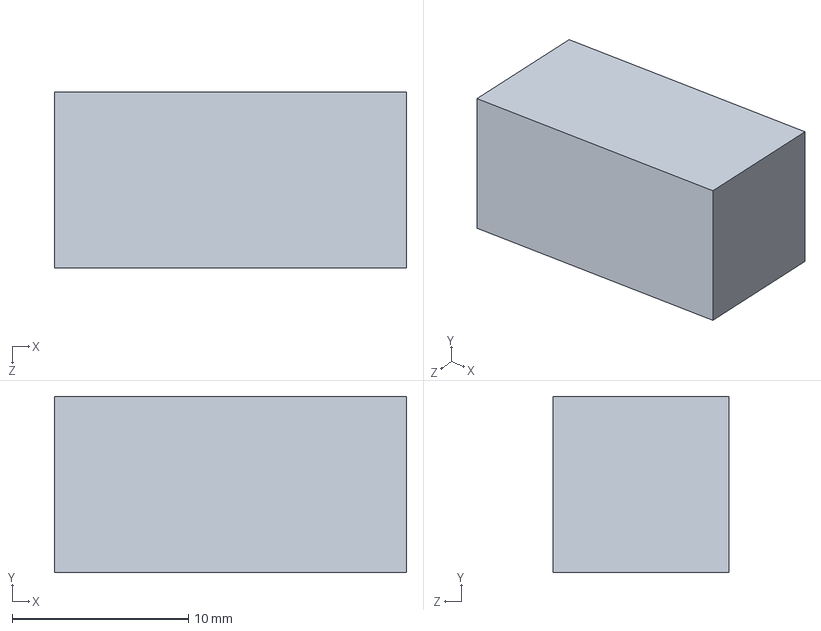
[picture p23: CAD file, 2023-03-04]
Analysis/PED_Sensor.SLDPRT
20.0 x 10.0 x 10.0 mm

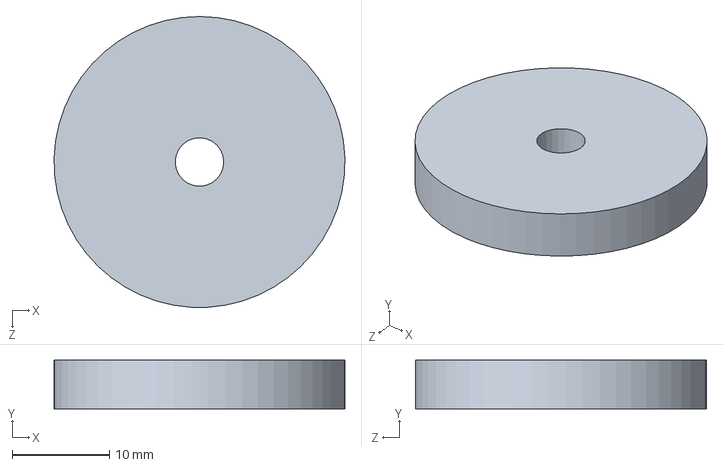
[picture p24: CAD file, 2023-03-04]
Analysis/PED_COIL.SLDPRT
30.0 x 5.00 x 30.0 mm

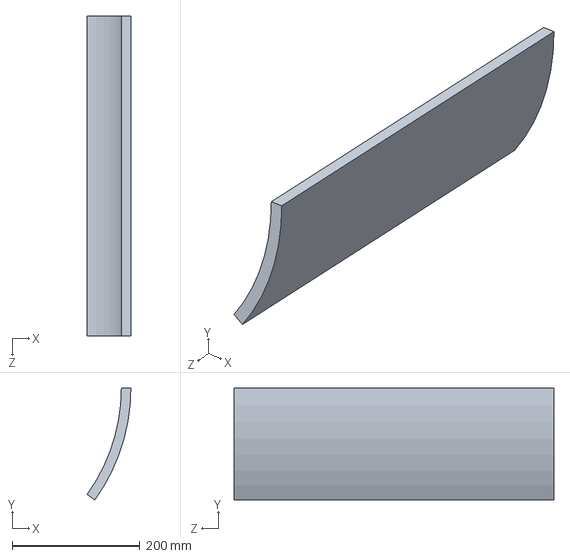
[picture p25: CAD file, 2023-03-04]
Analysis/SHIPHULL.SLDPRT
68.5 x 175.0 x 500.0 mm
